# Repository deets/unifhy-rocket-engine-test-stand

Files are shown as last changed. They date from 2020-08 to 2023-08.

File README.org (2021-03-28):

* UNIFHY - universeller Prüfstand für Feststoff- und Hybridmotoren

Ziel dieses Projektes ist die Entwicklung eines preiswerten
Prüfstandes mit einem Preis von maximal 500 EUR.

Der Prüfstand besteht aus drei Modulen:

 - Modul 1: einem aus ITEM Prüfbalken bestehenden mechanischen Aufbau.
 - Modul 2: einer Prüfbox zur Datenaufnahme, Speicherung, Übermittlung und
   gegebenenfalls Fernsteuerung.
 - Modul 3: einer Software zur Konfiguration, Datenerfassung und Auswertung von Modul 2.

Hier die [[file:doc/Pruefstand_UNIFHY.pdf][Anforderungen erhoben am 22.02.2020]].

** Modul 1 - Teststand

Ein Aufbau des Testands von Andreas:

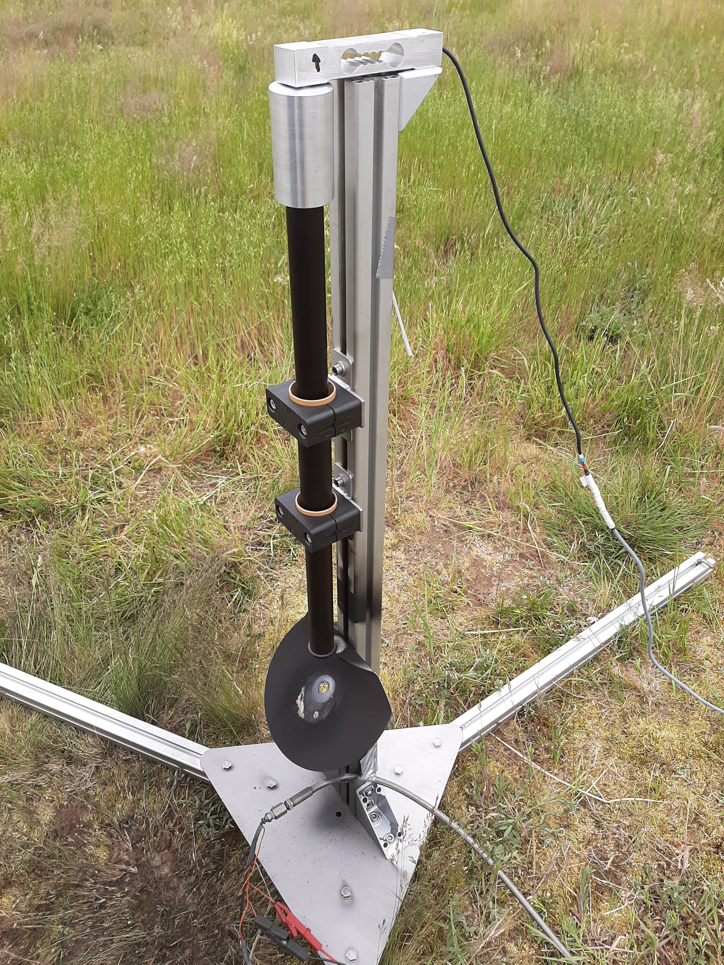
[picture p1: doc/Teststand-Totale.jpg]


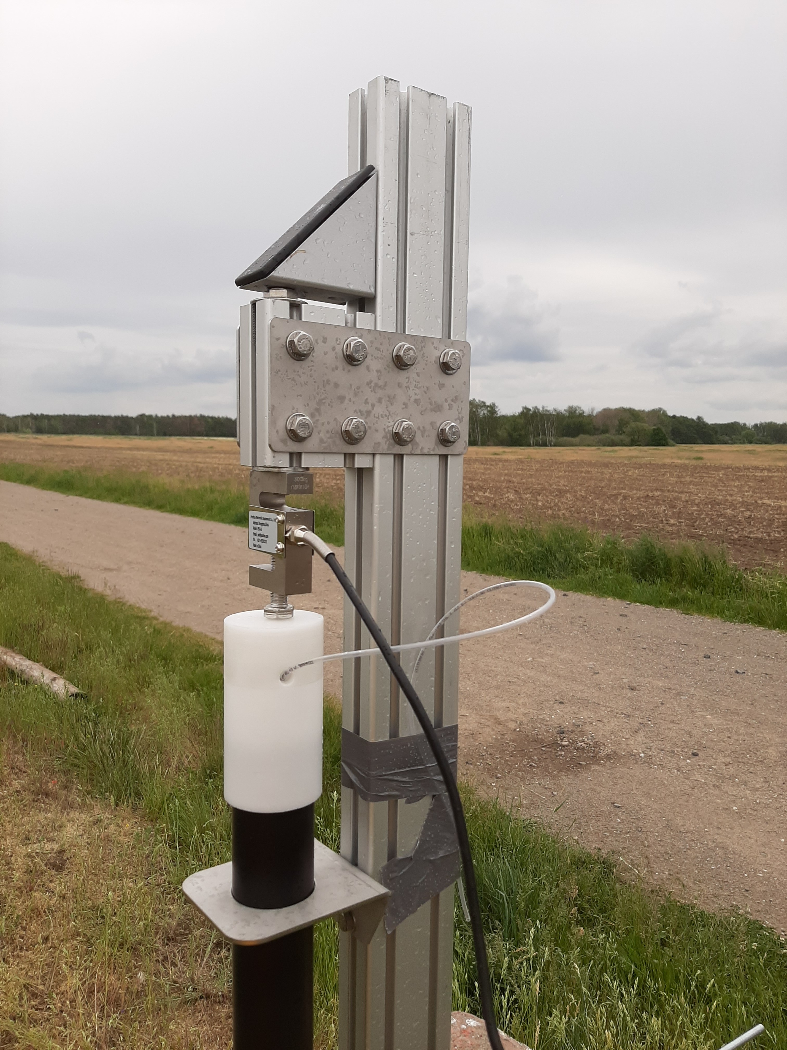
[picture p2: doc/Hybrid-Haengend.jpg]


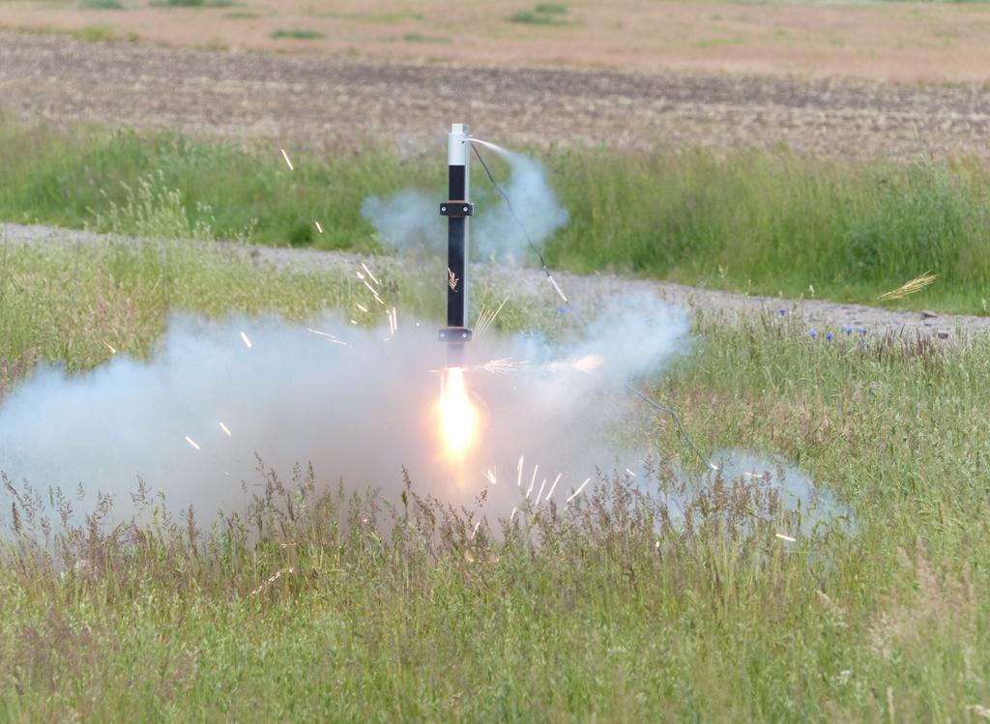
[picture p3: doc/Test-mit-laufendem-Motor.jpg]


** Modul 2 - Firmware

*** ADS1256 Breakout Board

Pin out of the breakout board as seen from top with control interface
to the left:

|-----+----------+---------|
| Pin | Function | P2 Eval |
|-----+----------+---------|
|   1 | PDWN     |      21 |
|   2 | CS_      |      20 |
|   3 | DRDY     |      19 |
|   4 | DOUT     |      17 |
|   5 | DIN      |      18 |
|   6 | SCLK     |      16 |
|   7 | GND      |     GND |
|   8 | 5V       |     EXT |
|-----+----------+---------|

#+attr_html: :width 400 px
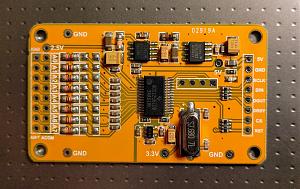
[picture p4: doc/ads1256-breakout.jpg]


** GIT Konfiguration

Wir arbeiten mit einem [[https://medium.com/singlestone/a-git-workflow-using-rebase-1b1210de83e5][rebase]] basierten GIT workflow. Dazu ist es
hilfreich eine Reihe von Einstellungen vorzunehmen. Die folgenden
Kommandos werden in einer Shell eingegeben, und man muss sich in
der Arbeitskopie befinden:

#+begin_src bash
git config pull.rebase true
#+end_src

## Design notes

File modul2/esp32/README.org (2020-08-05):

* Unifhy ESP32

A small test of the realtime capabilities of the ESP32 whilst
peforming writes to an SD-card and running a WIFI connection.

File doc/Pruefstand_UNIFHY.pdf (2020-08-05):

## Anforderungen an einen universellen Prüfstand für Feststoff- und Hybridmotoren

### Arbeitstitel: UNIFHY, Stand: 22.02.2020

Grundsätzliches:
–Materialpreis max. EUR 500,-
–Der Prüfstand besteht aus ITEM-Prüfbalken (Modul 1), Prüfbox für den Feldeinsatz (Modul 2) und Konfigurations- und Auswertesoftware für PC (Modul 3)
–Der Prüfbalken soll durch verschiedene Aufnahmen sowohl senkrecht, als auch waagerecht und „über Kopf“ positioniert werden können.
–Die Prüfbox soll sowohl alleine (mit kleinem LC-Display und Menüsteuerung, ähnlich der vieler 3D-Drucker), als auch mit Funk- oder USB-Verbindung zu einem Laptop, auf dem Modul 3 läuft, nutzbar sein.
–Bohrungen, Durchgänge, Steckverbindungen, Aufnahmen sollen standardisiert (und wetterfest) sein.
–aktuell mögliche Anzahl an Prüfständen: 7
–Für die Bedienung des Prüfstandes (inkl. Software) soll ein Tutorial geschrieben werden.
–Eine möglichst lange gesicherte Verfügbarkeit von Ersatzteilen (auch im Elektronik-Bereich) sollte gewährleistet sein.
–Der Prüfstand soll leicht auf- und abzubauen sein und bei Transport und Lagerung wenig Platz beanspruchen.

Mechanik:
– Aufbau auf ITEM-Profil 40 mm * 80 mm.
– Fußkonstruktion individuell, abhängig davon, wie der Motor ausgerichtet sein soll.
– Motorbefestigung mit Schellen und passgenauen Ringen, dadurch auch Zentrierung des Motors unter dem Biegebalken.
– Ein Überlastungsschutz für den Biegebalken ist sinnnvoll / ggf. auch nicht sinnvoll, wenn der Biegebalken billig und leicht auszutauschen ist?
– Befestigung des Biegebalkens am ITEM-Profil
– Verankerung der Fußkonstruktion (individuell), Verspannung des ITEM-Profils
– leichter Aufbau, sichere Ersatzteilbeschaffung für die nächsten Jahre

Elektronik:
– Messbereiche: bis 2000 N, bis 500 N, bis 10 N (jeweils mit einem für diesen Messbereich geeigneten Biegebalken/DMS)
– Arduino-basiert - Mega, Maple oder Due?
–Aufzeichnungsrate: bis 2000/s
–Auflösung: min. 12 bit
- 4 Messkanäle: Schub, Brennkammerdruck, Tankdruck, Temperatur – RTC
– Optional: Preview der Schubkurve über einen Bondrucker

Software:
– Es soll ein Programm (Modul 3) geschrieben werden, das sowohl die Konfiguration der Prüfbox (Modul 2), als auch die Datenerfassung während des Tests, als auch die Auswertung der Schubkurven (einschließlich erzeugen einer *.eng-Datei) gestattet und zudem bedienerfreundlich ist.
– Die Auswertung der Schubkurve soll weitestgehend automatisiert sein, bestimmte Punkte (s. Anlage 1) sollen aber auswählbar sein.
– Der Aufzeichnungsbeginn soll einstellbar sein, ebenso das Aufzeichnungsende. Eine automatische Aufzeichnung der Schubdaten mehrere Sekunden VOR Motoranzündung soll möglich sein.
– Ein weiteres Programm ist notwendig für den Betrieb der Prüfbox (Modul 2).
– Die PC-Software (Modul 3) soll den Benutzer entlang einer Checkliste vom Kalibrieren des Prüfstandes über den Motortest bis zur Auswertung führen.
– Anzündung des Motors wahlweise über die PC-Software (Modul 3) ODER manuell.
– Als Startsignal für die Datenaufzeichnung soll sowohl ein Messwert (z.B. F > 1 N), als auch das manuelle Anzündsignal (Startknopf), als auch eine Benutzereingabe (zum Testen) möglich sein. – Teilautomatische, software-geführte Kalibrierung des Prüfstandes mit drei geeigneten Massestücken.
– Speicherung der Rohdaten als ASCII-Datei. Ebenso Datenübertragung.
– „Nullsetzen“ muss möglich sein.
– Speicherung aller Rohdaten auf SD-Karte in Modul 2; während des Tests werden nur die wichtigsten Daten bzw. eine reduzierte Datenmenge (z.B. jeder 10. Messwert) in Echtzeit an Modul 3 übertragen.
– Eine „Fernsteuerung“ von Modul 2 soll möglich sein (Funk / Leitung / WLAN?).

Anlage 1

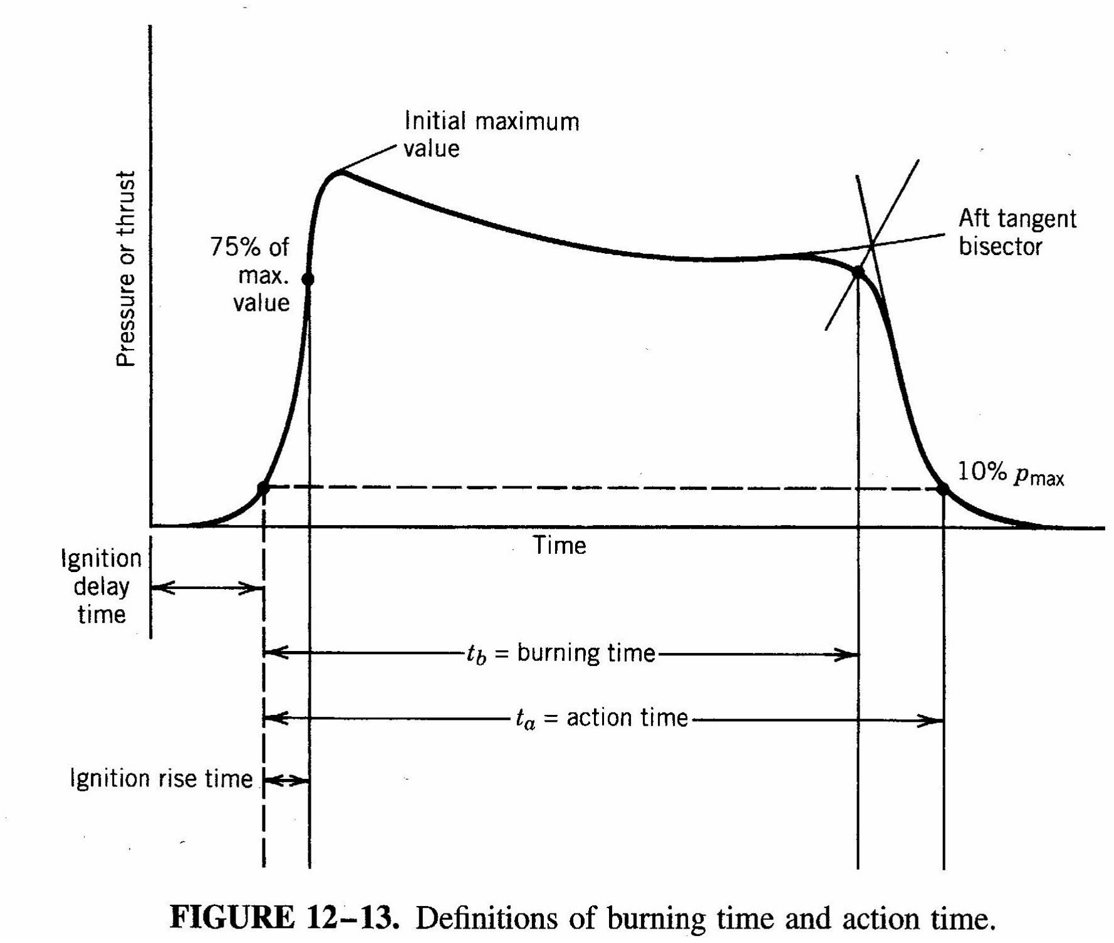
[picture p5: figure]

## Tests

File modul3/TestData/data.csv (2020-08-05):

Schub_x | Schub_y
0.0611 | -198.3902
0.1235 | -205.9467
0.1348 | -211.5601
0.1462 | -197.7425
0.1575 | -175.9366
0.1688 | -151.324
0.1802 | -170.1073
0.1915 | -187.8111
0.2028 | -197.3107
0.2142 | -248.479
0.2255 | -194.504
0.2368 | -218.4689
0.2482 | -233.1501
0.2595 | -201.1969
0.2708 | -216.7417
0.2822 | -199.9015
0.2935 | -233.5819
0.3048 | -140.529
0.3162 | -209.617
0.3275 | -203.3559
0.3389 | -129.5181
0.3502 | -291.659
0.3615 | -123.0411
0.3729 | -220.412
0.3842 | -181.3341
0.3955 | -152.4035
0.4069 | -281.0799
0.4182 | -148.0855
0.4295 | -252.1493
0.4409 | -136.211
0.4522 | -160.1759
0.4635 | -210.0488
0.4749 | -106.6327
0.4862 | -276.7619
0.4975 | -135.5633
0.5089 | -233.366
0.5202 | -206.8103
0.5316 | -153.2671
0.5429 | -264.6715
0.5542 | -120.6662
0.5656 | -285.8297
0.5769 | -169.4596
0.5882 | -183.4931
0.5996 | -239.843
0.6109 | -106.6327
0.6222 | -242.8656
0.6336 | -107.7122
0.6449 | -191.0496
0.6562 | -171.8345
0.6676 | -96.9172
0.6789 | -180.0387
0.6903 | -17.6819
0.7016 | -168.8119
0.7129 | -38.6242
0.7243 | -51.3623
0.7356 | -86.554
0.7469 | 75.1551
0.7583 | -69.0661
0.7696 | 91.7794
0.7809 | 29.3843
0.7924 | 29.6002
0.804 | 50.5425
0.8157 | -103.826
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

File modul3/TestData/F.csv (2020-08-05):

# Observable : F
# Unit       : none
# ID         : 0
#
# Calibration
#
# fitting function : linear
# parameters :
#
# a*x+b
# a = 0.00044840
# b = -9.76000000
# recorded events : 137071
#
0.060900  20.898902
0.123100  20.878275
0.134400  20.933877
0.145700  20.855407
0.157000  20.810567
0.168300  20.882311
0.179600  20.928944
0.190900  20.901144
0.202100  20.913250
0.213400  20.939706
0.224700  20.883656
0.236000  20.896211
0.247300  20.908318
0.258600  20.876482
0.269900  20.800254
0.281200  20.817293
0.292500  20.858994
0.303800  20.930290
0.315100  20.962126
0.326400  20.898902
0.337700  20.946880
0.349000  20.998446
0.360300  20.953606
0.371600  20.847784
0.382900  20.828054
0.394200  20.926254
0.405500  20.839713
0.416800  20.850923
0.428100  20.869307
0.439300  20.856304
0.450600  20.906524
0.461900  20.951813
0.473200  21.011898
0.484500  20.959436
0.495800  20.878724
0.507100  20.893521
0.518400  20.876033
0.529700  20.878724
0.541000  20.894418
0.552300  20.833884
0.563600  20.928048
0.574900  20.945984
0.586200  20.911457
0.597500  20.885450
0.608800  20.972439
0.620100  20.996653
0.631400  20.983201
0.642700  20.910112
0.654000  20.839264
0.665300  20.955848
0.676600  20.974681
0.687800  20.887243
0.699100  20.908318
0.710400  20.899798
0.721700  20.913250
0.733000  20.933428
0.744300  20.934325
0.755600  20.900247
0.766900  20.902040
0.778200  20.853165
0.789700  20.848232
0.801300  20.918183
0.812900  20.915941
0.824400  20.912354
0.836000  20.877827
0.847600  20.828503
0.859100  20.858097
0.870700  20.880517
0.882300  20.906524
0.893800  20.891279
0.905400  20.882311
0.917000  20.954055
0.928600  20.955400
0.940100  20.971094
0.951700  20.993066
0.963300  20.876482
0.974800  20.842403
0.986400  20.906076
0.998000  20.954952
1.009500  20.901592
1.021100  20.888588
1.032600  20.925357
1.044200  20.882311
1.055800  20.923115
1.067400  20.921770
1.078900  20.908766
1.090500  20.917734
1.102100  20.885898
1.113600  20.870652
1.125200  20.963471
1.136800  20.936567
1.148400  20.898902
1.159900  20.914596
1.171500  20.842852
1.183100  20.898902
1.194600  20.947329
1.206200  20.967058
1.217800  20.963471
1.229300  20.952710
1.240900  20.951364
1.252500  20.923115
1.264000  20.870652
1.275600  20.822674
1.287200  20.787250
1.298800  20.890382
1.310300  20.983201
1.321900  20.950916
1.333500  20.902937
1.345000  20.872446
1.356600  20.915044
1.368100  20.931186
1.379700  20.923564
1.391300  20.939706
1.402900  20.871998
1.414400  20.895314
1.426000  20.941051
1.437600  20.902040
1.449100  20.914147
1.460700  20.833884
1.472300  20.827158
1.483800  20.915492
1.495400  20.932980
1.507000  20.938809
1.518500  20.924460
1.530100  20.931186
1.541700  20.935670
1.553300  20.949571
1.564800  20.971542
1.576400  20.929393
1.588000  20.905628
1.599500  20.915044
1.611100  20.932980
1.622700  20.892176
1.634200  20.932083
1.645800  20.994859
1.657400  20.950019
1.668900  20.918631
1.680500  20.901144
1.692100  20.858097
1.703600  20.845542
1.715200  20.887243
1.726800  20.921770
1.738400  20.924012
1.749900  20.940154
1.761500  20.902937
1.773100  20.897556
1.784600  20.922667
1.796200  20.941500
1.807800  20.905179
1.819300  20.952710
1.830900  20.959884
1.842500  20.973784
1.854100  20.946432
1.865600  20.827158
1.877200  20.873343
1.888800  20.914147
1.900300  20.939258
1.911900  20.906524
1.923500  20.876482
1.935000  20.886795
1.946600  20.952710
1.958200  20.959884
1.969700  20.912802
1.981300  20.941051
1.992900  20.927151
2.004500  20.905179
2.016000  20.956745
2.027600  21.007863
2.039100  20.943293
2.050700  21.008760
2.062300  20.976475
2.073900  20.911905
2.085400  20.945087
2.097000  20.853165
2.108600  20.910560
2.120100  20.930738
2.131700  20.940603
2.143300  20.937912
2.154900  20.962126
2.166400  20.947777
2.178000  20.928944
2.189600  20.941051
2.201100  21.002930
2.212800  20.967507
2.224300  20.916389
2.235800  20.958987
2.247400  20.940603
2.259000  20.967058
2.270600  21.002482
2.282100  21.060774
2.293700  20.980959
2.305300  20.936119
2.316800  20.956297
2.328400  20.930738
2.340000  20.925806
2.351500  20.918631
2.363100  20.914596
2.374700  20.933877
2.386200  20.939706
2.397800  20.888588
2.409400  20.846887
2.421000  20.917734
2.432500  20.979165
2.444100  20.976923
2.455700  20.923564
2.467200  20.909215
2.478800  20.902489
2.490400  20.918631
2.501900  20.892176
2.513500  20.950468
2.525100  21.003379
2.536600  21.006966
2.548200  21.039251
2.559800  20.961678
2.571300  20.920425
2.582900  20.918183
2.594500  20.919080
2.606100  20.997550
2.617600  21.013692
2.629200  20.944190
2.640800  20.885450
2.652300  20.936119
2.663900  20.985891
2.675500  20.950019
2.687200  20.926702
2.698600  20.922667
2.710200  20.919528
2.721800  20.930738
2.733300  20.924012
2.744900  20.955400
2.756500  20.944638
2.768000  20.917734
2.779600  20.903386
2.791200  20.909663
2.802700  20.896211
2.814300  20.954503
2.825900  20.915941
2.837400  20.964368
2.849000  20.971542
2.860600  20.906973
2.872100  20.933428
2.883700  20.932980
2.895300  20.931186
2.906800  20.941948
2.918400  20.942845
2.930000  21.001585
2.941600  20.917286
2.953100  20.858994
2.964700  20.885898
2.976300  20.952710
2.987800  20.987236
2.999400  21.008311
3.011000  20.956745
3.022500  20.931186
3.034100  20.906524
3.045700  20.887692
3.057200  20.909215
3.068800  20.880966
3.080400  20.899350
3.091900  20.923115
3.103500  20.937464
3.115100  20.903834
3.126700  20.902489
3.138200  20.934325
3.149800  20.963023
3.161400  20.946880
3.173000  20.965265
3.184500  20.897108
3.196100  20.926702
3.207700  20.943293
3.219200  20.910112
3.230800  20.895314
3.242400  20.963023
3.253900  20.964816
3.265500  20.949571
3.277100  20.904731
3.288700  20.928048
3.300200  20.950468
3.311800  20.947777
3.323400  20.986340
3.334900  20.975578
3.346500  20.938809
3.358100  20.961678
3.369600  20.972439
3.381200  20.953606
3.392800  20.925357
3.404300  20.951813
3.415900  20.947777
3.427500  20.931186
3.439100  20.945984
3.450600  20.899350
3.462200  20.946880
3.473800  20.948674
3.485300  20.960781
3.496900  20.944190
3.508500  20.935670
3.520100  20.866617
3.531600  20.925357
3.543200  20.912354
3.554800  20.981856
3.566300  20.974681
3.577900  20.940154
3.589500  20.930290
3.601000  20.939258
3.612600  20.913699
3.624200  20.902040
3.635700  20.911905
3.647300  20.948226
3.658900  20.905628
3.670500  20.834780
3.682000  20.891727
3.693600  20.938361
3.705200  20.909215
3.716700  20.931635
3.728300  20.896211
3.739900  20.894418
3.751400  20.985443
3.763000  20.967955
3.774600  20.956745
3.786100  20.958987
3.797700  20.925357
3.809300  20.932980
3.820800  20.939706
3.832400  20.900695
3.844000  20.937464
3.855500  21.012347
3.867100  20.965713
3.878700  20.984994
3.890300  20.958090
3.901800  20.962126
3.913400  20.972888
3.925000  20.955400
3.936500  20.941500
3.948100  20.908318
3.959700  20.925806
3.971200  20.958539
3.982800  20.963023
3.994400  21.013244
4.005900  20.972439
4.017500  20.872446
4.029100  20.915492
4.040600  20.991720
4.052200  20.978717
4.063800  20.963920
4.075300  20.931186
4.086900  20.941051
4.098500  20.934774
4.110100  20.896660
4.121700  20.871101
4.133200  20.916838
4.144800  20.928496
4.156300  20.876482
4.167900  20.871998
4.179500  20.929393
4.191100  20.913699
4.202600  20.859891
4.214200  20.972439
4.225800  20.984546
4.237300  20.985443
4.248900  20.988133
4.260500  20.926254
4.272000  20.899798
4.283600  20.898902
4.295200  20.962126
4.306700  20.982304
4.318300  21.036560
4.329900  20.984098
4.341500  20.945535
4.353000  20.933428
4.364600  20.934325
4.376200  20.937912
4.387700  21.019970
4.399300  20.967955
4.410900  20.916838
4.422400  20.921770
4.434000  20.935222
4.445600  20.920873
4.457100  20.897108
4.468700  20.938809
4.480300  20.896660
4.491900  20.942845
4.503400  21.029834
4.515000  21.063016
4.526600  20.982304
4.538100  20.876033
4.549700  20.853165
4.561300  20.917734
4.572800  20.901144
4.584400  20.922667
4.596100  20.896211
4.607600  20.937016
4.619100  20.968404
4.630700  20.952261
4.642300  20.936567
4.653800  20.989478
4.665400  21.002930
4.677000  20.999343
4.688600  20.871998
4.700100  20.853613
4.711700  20.906973
4.723300  20.955848
4.734800  20.937912
4.746400  20.935670
4.758000  20.931635
4.769500  20.939706
4.781100  20.991720
4.792700  20.958987
4.804300  20.931186
4.815800  20.942396
4.827400  20.996653
4.839000  20.987685
4.850500  20.923115
4.862100  20.912802
4.873700  20.954055
4.885200  20.994859
4.896800  20.952710
4.908400  20.905179
4.920000  20.933428
4.931500  20.933877
4.943100  20.899798
4.954700  20.937912
4.966200  20.960781
4.977800  20.887243
4.989400  20.941500
5.001000  20.968404
5.012500  20.931635
5.024100  20.864823
5.035600  20.908766
5.047200  20.930738
5.058800  20.867962
5.070500  20.862133
5.081900  20.899798
5.093500  20.976475
5.105000  20.961229
5.116600  20.924460
5.128200  20.904282
5.139800  20.898005
5.151300  20.893969
5.162900  20.941500
5.174500  20.961229
5.186000  20.982304
5.197600  20.993514
5.209200  20.984546
5.220700  20.979614
5.232300  20.939706
5.243900  20.948226
5.255400  20.979165
5.267000  20.944190
5.278600  20.941500
5.290200  20.910560
5.301700  20.905628
5.313300  20.878724
5.324900  20.898902
5.336400  20.909215
5.348000  20.954055
5.359600  20.943293
5.371100  20.889934
5.382700  20.866168
5.394300  20.871998
5.405800  20.930290
5.417400  20.901144
5.429000  20.967955
5.440500  20.970646
5.452100  20.914596
5.463700  20.891279
5.475200  20.891727
5.486800  20.918631
5.498400  20.980510
5.510000  20.976923
5.521500  20.987236
5.533100  20.930738
5.544700  20.970197
5.556200  20.961229
5.567800  20.964368
5.579400  20.964816
5.590900  20.856304
5.602500  20.863926
5.614100  20.943293
5.625700  20.882311
5.637200  20.957194
5.648800  21.028938
5.660400  21.020418
5.671900  20.959436
5.683500  20.951813
5.695100  20.867962
5.706600  20.897108
5.718200  20.946880
5.729800  20.959884
5.741400  20.911457
5.752900  20.917734
5.764500  20.905179
5.776100  20.947777
5.787600  20.908766
5.799200  20.877827
5.810800  20.968404
5.822300  20.935222
5.833900  20.931186
5.845500  20.915941
5.857100  20.945087
5.868600  20.952261
5.880200  20.933877
5.891700  20.957194
5.903300  20.993066
5.914900  20.873343
5.926500  20.903386
5.938000  20.964816
5.949600  20.951364
5.961200  20.980510
5.972700  20.958539
5.984300  20.943293
5.995900  20.962574
6.007500  20.972888
6.019000  20.957642
6.030700  20.896211
6.042100  20.816396
6.053700  20.893072
6.065300  20.945984
6.076800  20.962126
6.088400  20.907870
6.100000  20.904731
6.111600  20.919528
6.123100  20.908318
6.134700  20.965265
6.146300  20.983201
6.157800  20.941948
6.169400  20.945087
6.181000  20.986340
6.192600  20.928496
6.204100  20.896660
6.215700  20.893969
6.227300  20.921322
6.238800  20.950468
6.250400  20.919080
6.262000  20.939706
6.273500  20.950019
6.285100  20.897556
6.296700  20.940603
6.308200  20.892176
6.319800  20.881862
6.331400  20.977820
6.342900  20.968852
6.354500  20.936119
6.366100  20.923115
6.377700  20.968404
6.389200  20.979614
6.400800  20.988582
6.412400  20.987685
6.423900  20.869307
6.435500  20.916838
6.447100  20.918631
6.458600  20.903386
6.470200  20.892176
6.481800  20.878724
6.493300  20.935222
6.504900  20.901592
6.516500  20.868859
6.528100  20.941948
6.539600  20.983201
6.551200  20.998895
6.562800  20.980510
6.574300  20.920425
6.585900  20.918631
6.597500  20.969749
6.609000  20.953158
6.620600  20.936567
6.632200  20.945087
6.643700  21.027592
6.655300  21.036560
6.666900  20.980510
6.678500  20.897108
6.690000  20.938361
6.701600  20.928496
6.713200  20.919528
6.724700  20.952710
6.736300  20.918631
6.747900  20.957642
6.759400  20.936119
6.771000  20.945984
6.782600  20.933428
6.794100  20.889934
6.805700  20.891279
6.817300  20.959884
6.828900  20.967058
6.840400  20.994411
6.852000  20.988133
6.863600  21.024454
6.875100  20.955400
6.886700  20.906524
6.898300  20.993514
6.909800  21.012795
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

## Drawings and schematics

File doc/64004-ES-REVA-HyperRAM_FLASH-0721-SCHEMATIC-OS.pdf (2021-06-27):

## HyperRAM and HyperFLASH

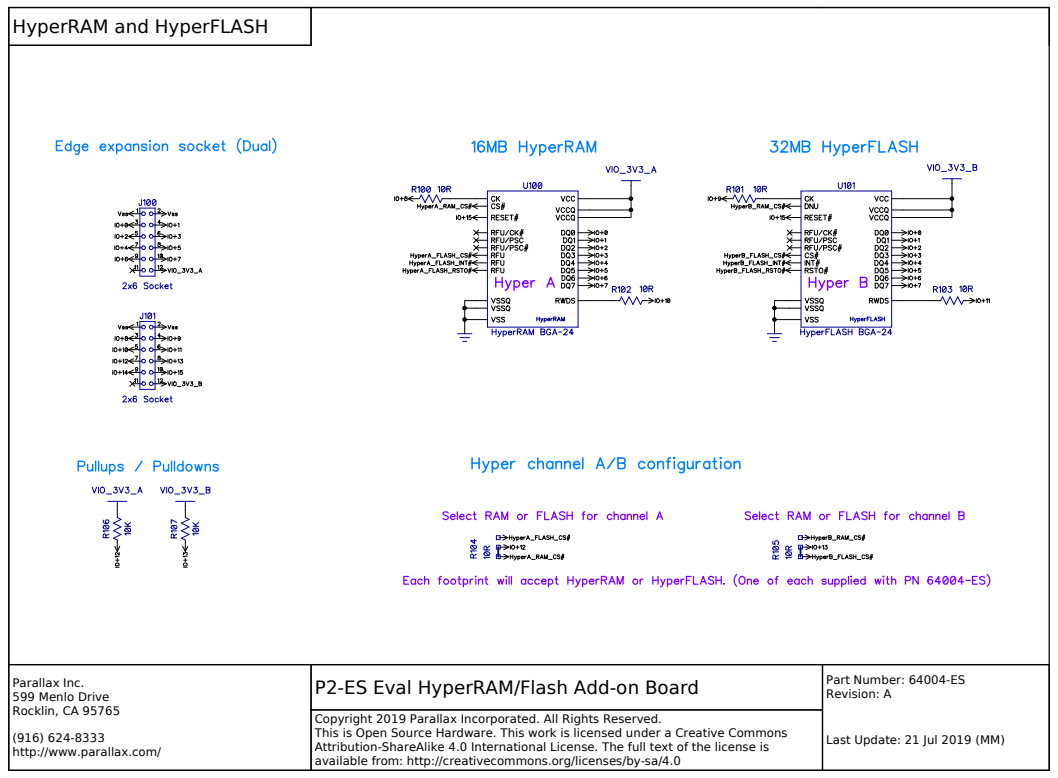
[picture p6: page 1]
P2-ES Eval HyperRAM/Flash Add-on Board; Part Number: 64004-ES; Revision: A; Parallax Inc. 599 Menlo Drive Rocklin, CA 95765

Copyright 2019 Parallax Incorporated. All Rights Reserved.
This is Open Source Hardware. This work is licensed under a Creative Commons
Attribution-ShareAlike 4.0 International License. The full text of the license is
available from: http://creativecommons.org/licenses/by-sa/4.0

http://www.parallax.com/

Last Update: 21 Jul 2019 (MM)

## Decoupling and Breakouts

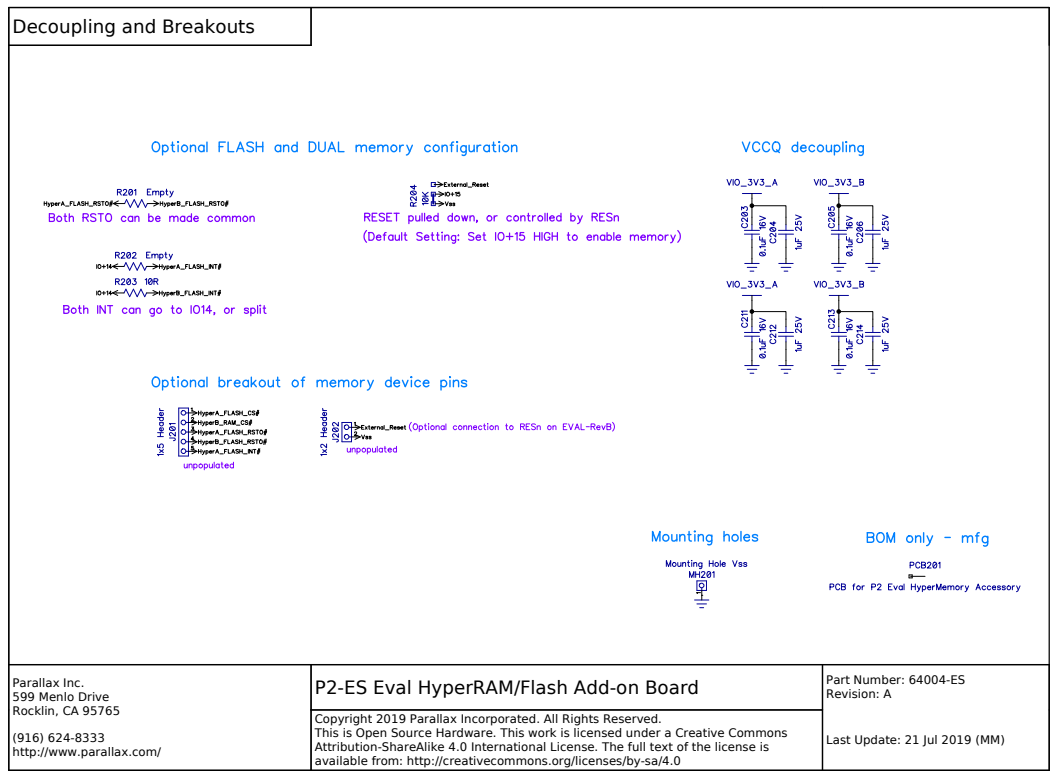
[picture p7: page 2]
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

## BOM

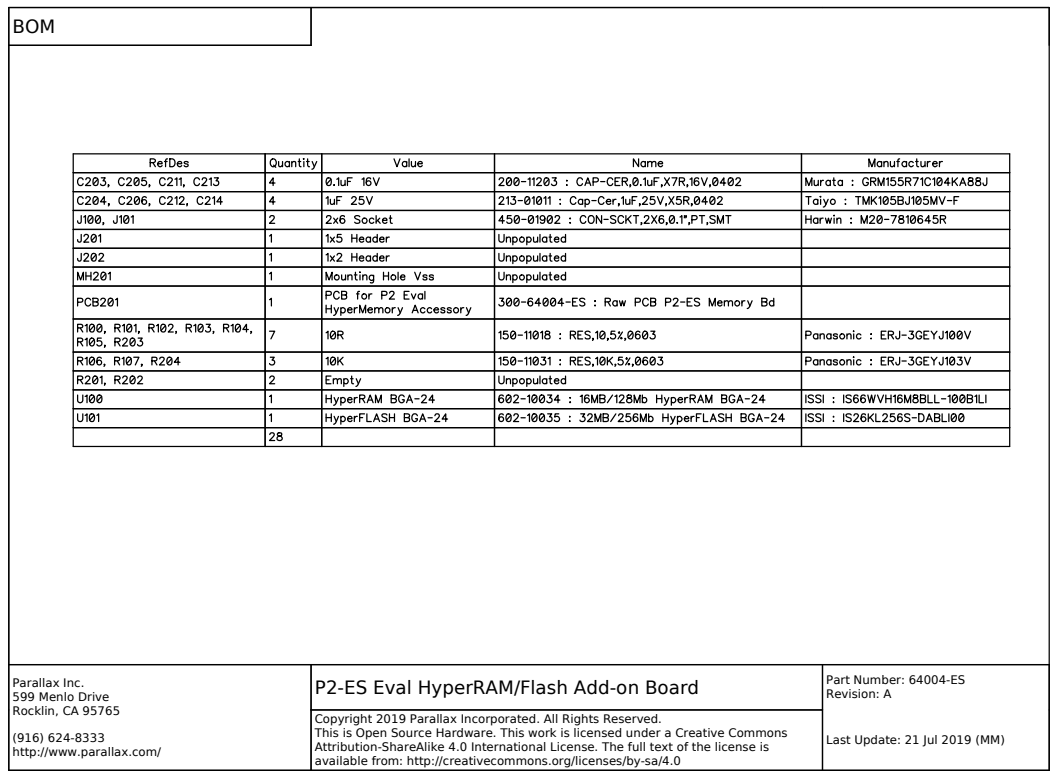
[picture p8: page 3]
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

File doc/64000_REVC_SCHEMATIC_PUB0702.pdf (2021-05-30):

## Microcontroller

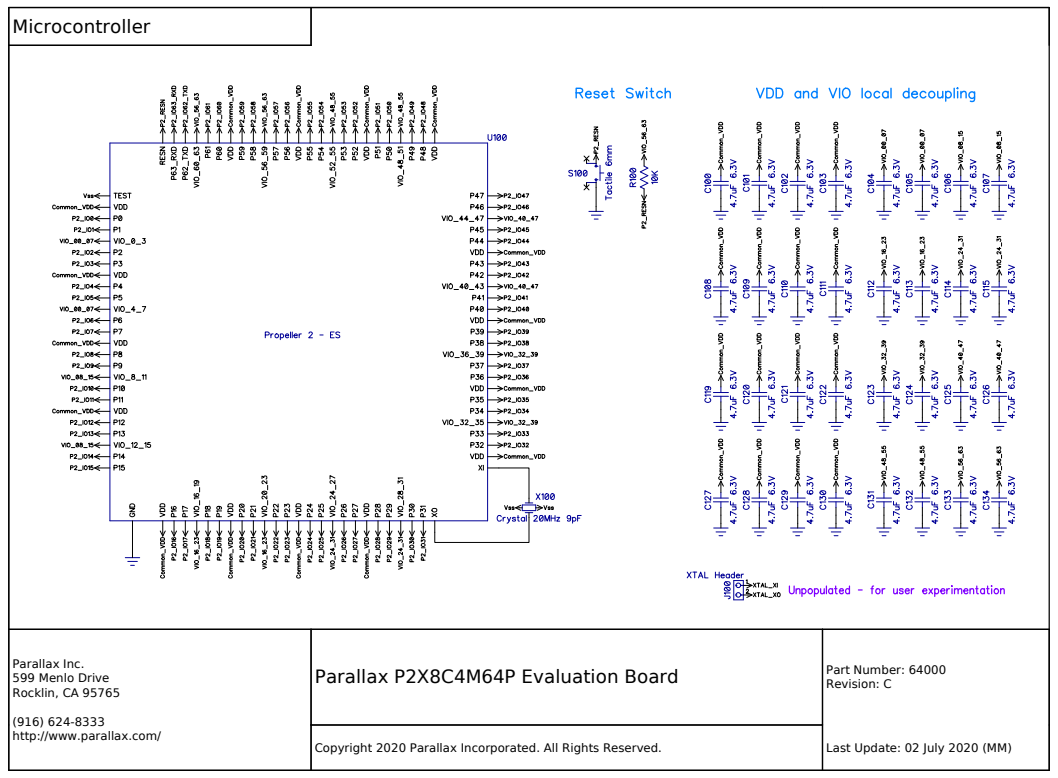
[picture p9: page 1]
Parallax P2X8C4M64P Evaluation Board; Part Number: 64000; Revision: C; Parallax Inc. 599 Menlo Drive Rocklin, CA 95765; Copyright 2020 Parallax Incorporated. All Rights Reserved.; Last Update: 02 July 2020 (MM)

http://www.parallax.com/

## I/O Headers

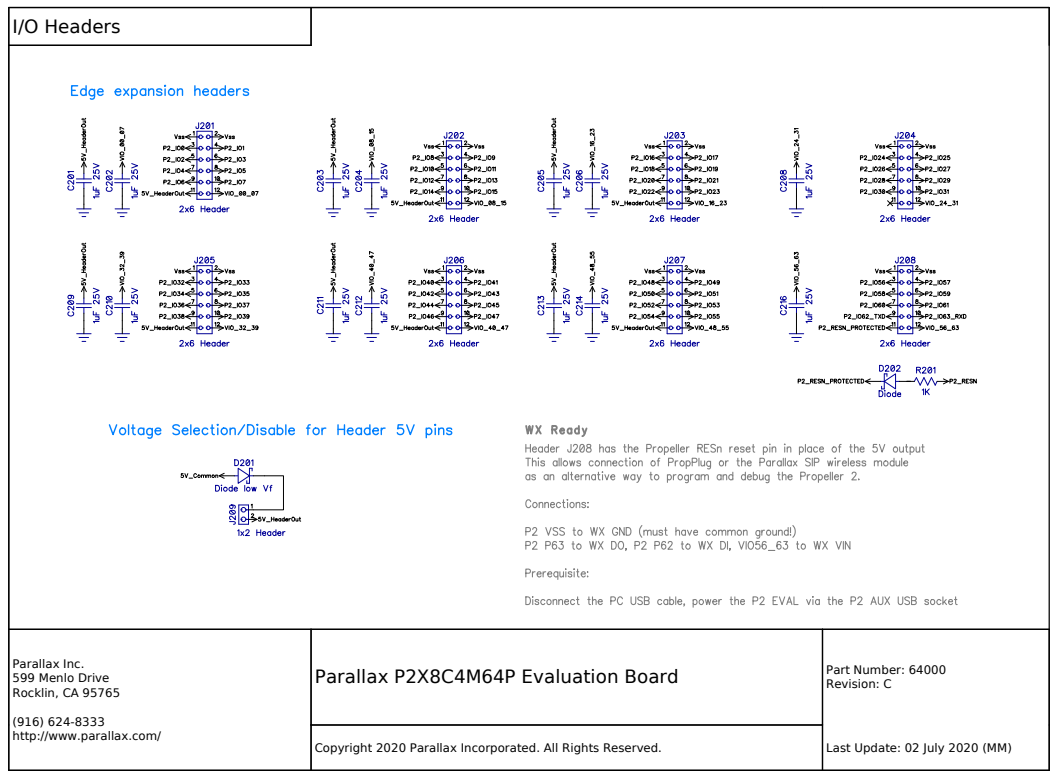
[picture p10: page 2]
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

## Memory

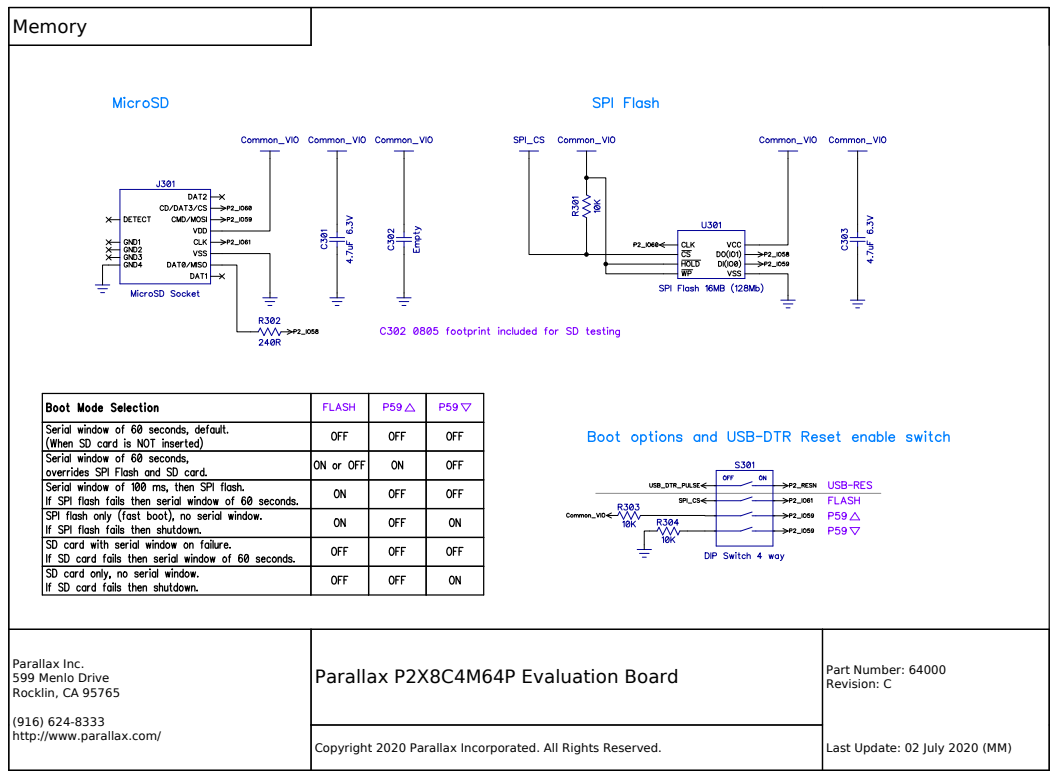
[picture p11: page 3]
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

## USB PC Socket

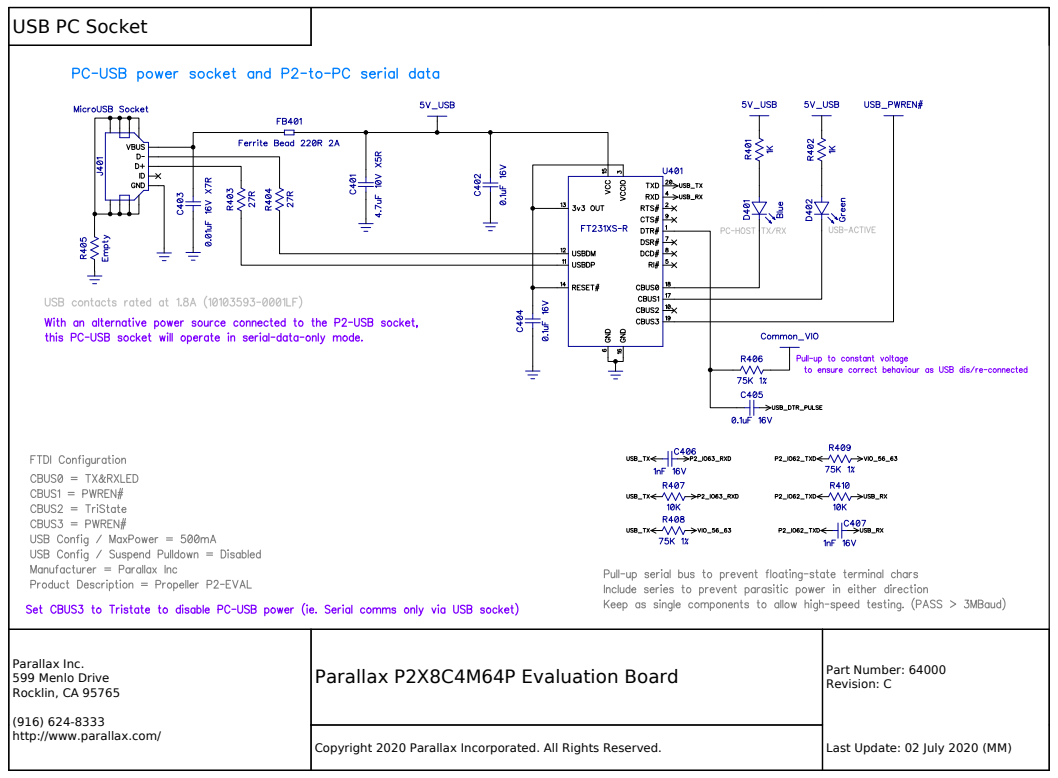
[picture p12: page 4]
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

## USB Aux Power Socket

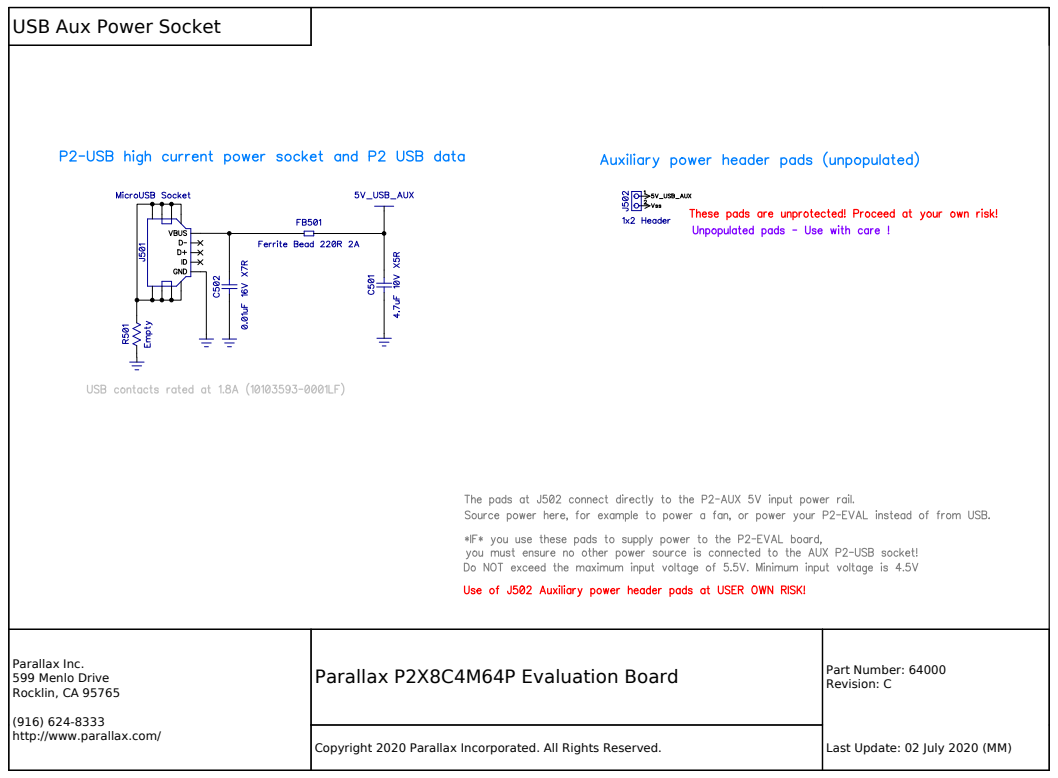
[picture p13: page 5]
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

## USB Current Limit and Logic

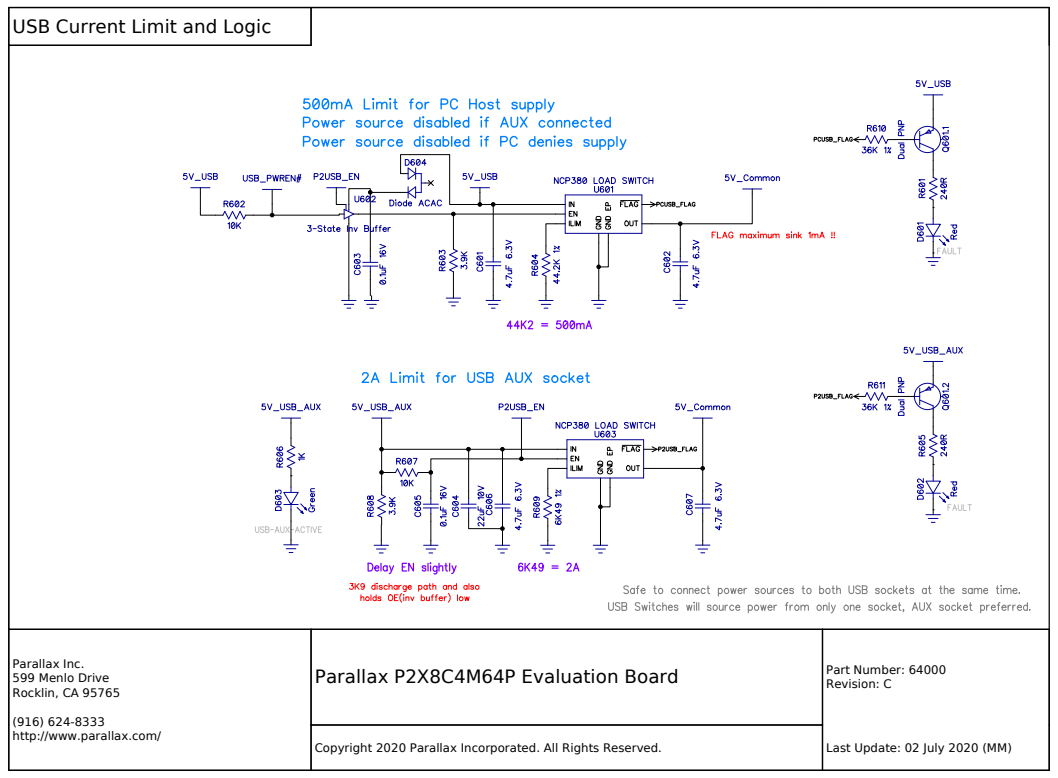
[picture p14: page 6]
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

## Common VDD 1V8

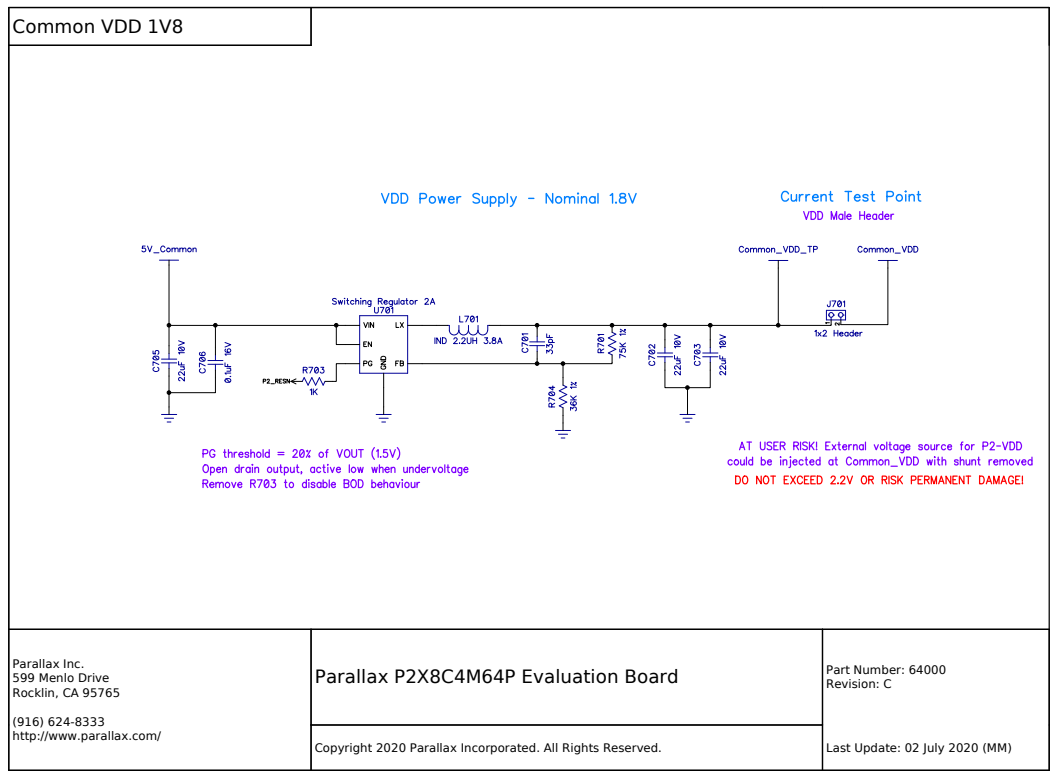
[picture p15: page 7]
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

## Common VIO 3V3

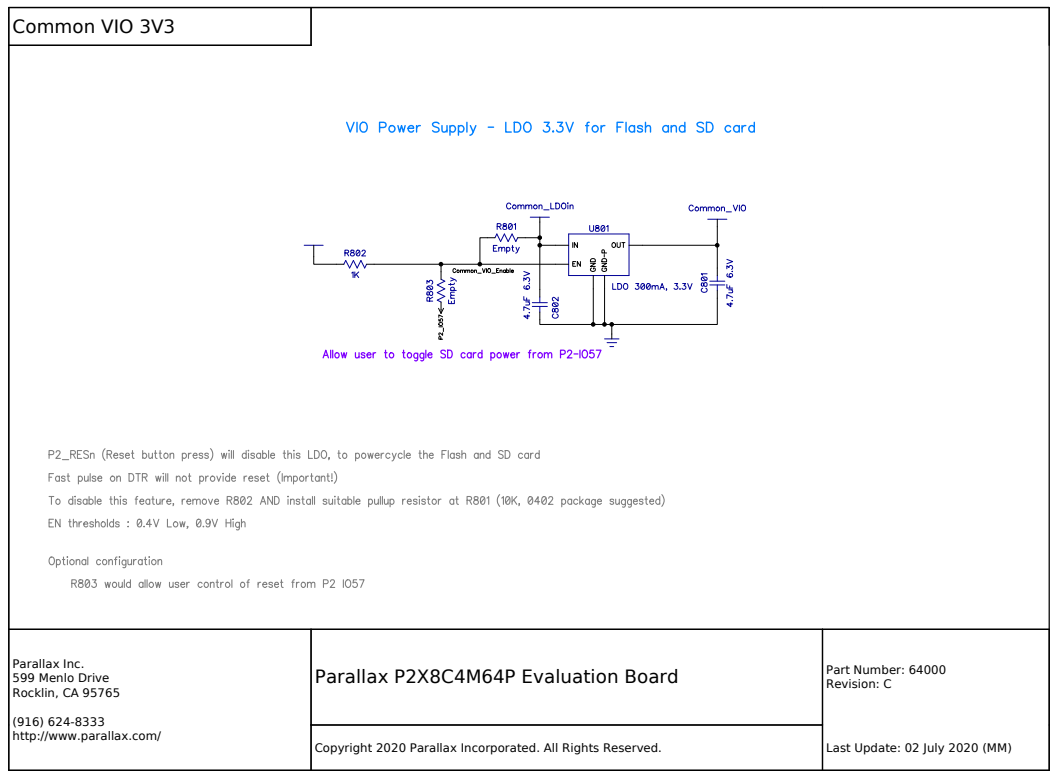
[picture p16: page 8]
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

## LDO 3V3

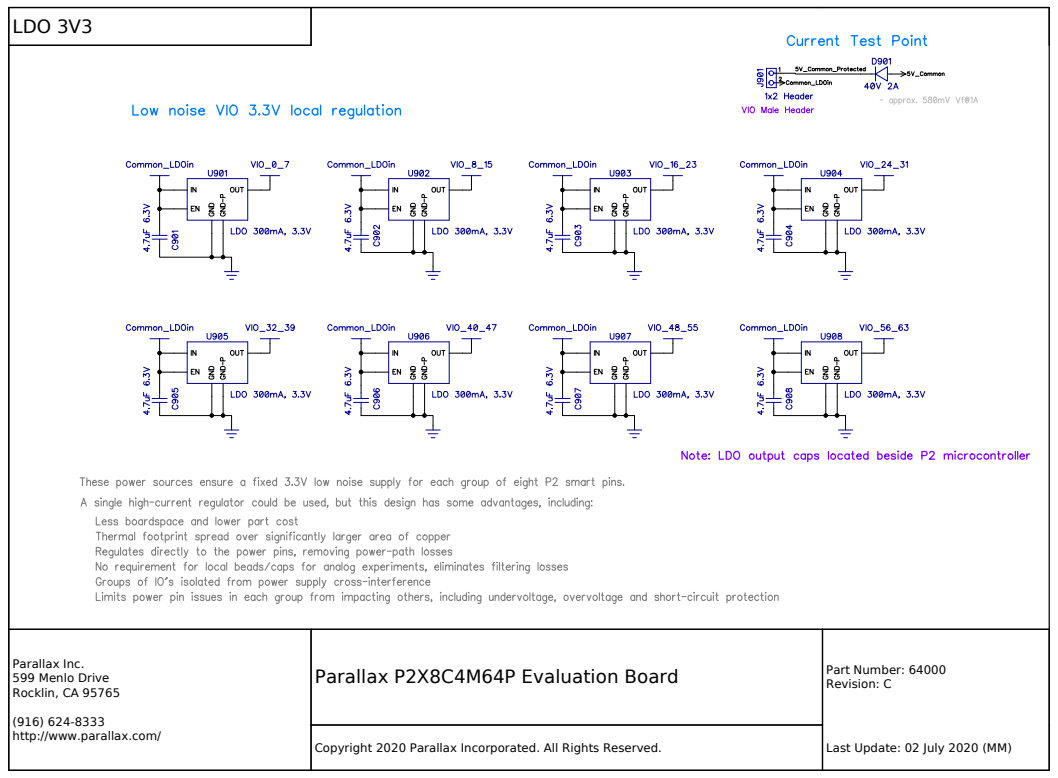
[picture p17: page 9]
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

## LEDs

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

## Misc

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

## BOM

Parallax P2X8C4M64P Evaluation Board | Part Number: 64000 Revision: C

Parallax Inc.
599 Menlo Drive
Rocklin, CA 95765


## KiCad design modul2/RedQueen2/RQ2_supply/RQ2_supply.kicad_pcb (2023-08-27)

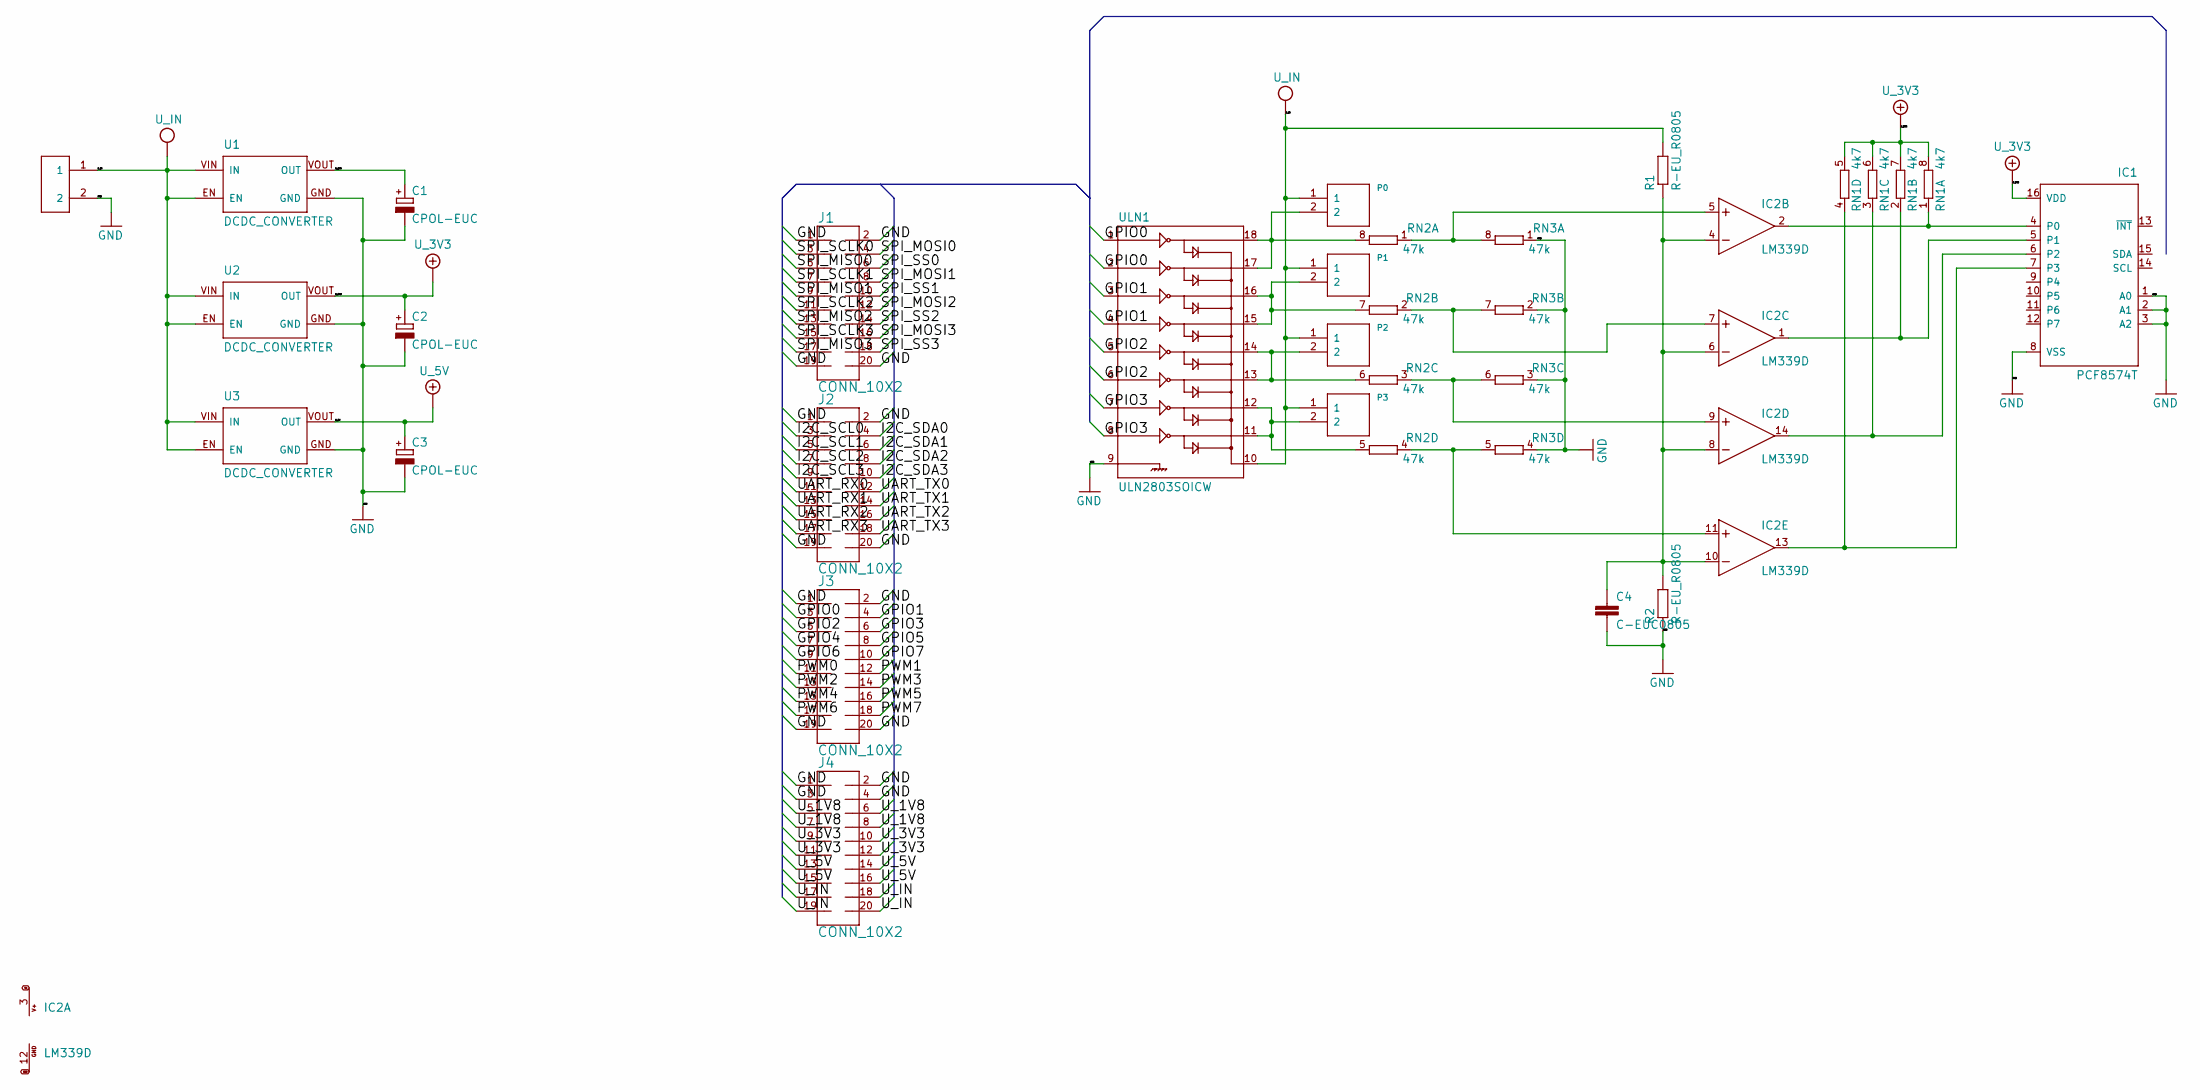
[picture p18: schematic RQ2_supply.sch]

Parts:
C1, C2, C3: CPOL-EUC; PANASONIC_C
C4: C-EUC0805; C0805
IC1: PCF8574T; SO16W
IC2: LM339D; SO14
J1, J2, J3, J4: CONN_10X2; 2X10
P0, P1, P2, P3: 2PIN; B2B-PH-K-S
R1, R2: R-EU_R0805; R0805
RN1: 4k7; 0603-ARV
RN2, RN3: 47k; 0603-ARV
U1, U2, U3: DCDC_CONVERTER
U$1: XT_CONN; XT30_PCB
ULN1: ULN2803SOICW; SO18L

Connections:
/GPIO0: J3.3, ULN1.1, ULN1.2
/GPIO1: J3.4, ULN1.3, ULN1.4
/GPIO2: J3.5, ULN1.5, ULN1.6
/GPIO3: J3.6, ULN1.7, ULN1.8
/GPIO4: J3.7
/GPIO5: J3.8
/GPIO6: J3.9
/GPIO7: J3.10
/I2C_SCL0: J2.3
/I2C_SCL1: J2.5
/I2C_SCL2: J2.7
/I2C_SCL3: J2.9
/I2C_SDA0: J2.4
/I2C_SDA1: J2.6
/I2C_SDA2: J2.8
/I2C_SDA3: J2.10
/PWM0: J3.11
/PWM1: J3.12
/PWM2: J3.13
/PWM3: J3.14
/PWM4: J3.15
/PWM5: J3.16
/PWM6: J3.17
/PWM7: J3.18
/SPI_MISO0: J1.5
/SPI_MISO1: J1.9
/SPI_MISO2: J1.13
/SPI_MISO3: J1.17
/SPI_MOSI0: J1.4
/SPI_MOSI1: J1.8
/SPI_MOSI2: J1.12
/SPI_MOSI3: J1.16
/SPI_SCLK0: J1.3
/SPI_SCLK1: J1.7
/SPI_SCLK2: J1.11
/SPI_SCLK3: J1.15
/SPI_SS0: J1.6
/SPI_SS1: J1.10
/SPI_SS2: J1.14
/SPI_SS3: J1.18
/UART_RX0: J2.11
/UART_RX1: J2.13
/UART_RX2: J2.15
/UART_RX3: J2.17
/UART_TX0: J2.12
/UART_TX1: J2.14
/UART_TX2: J2.16
/UART_TX3: J2.18
/U_1V8: C1.+, J4.5, J4.6, J4.7, J4.8, U1.VOUT (OUT)
GND: C1.-, C2.-, C3.-, C4.2, IC1.1 (A0), IC1.2 (A1), IC1.3 (A2), IC1.8 (VSS), IC2.12 (GND), J1.1, J1.2, J1.19, J1.20, J2.1, J2.2, J2.19, J2.20, J3.1, J3.2, J3.19, J3.20, J4.1, J4.2, J4.3, J4.4, R2.1, RN3.1, RN3.2 (1), RN3.3 (1), RN3.4 (1), U1.GND, U2.GND, U3.GND, U$1.2, ULN1.9
unnamed: C4.1, IC2.4 (-IN), IC2.6 (-IN), IC2.8 (-IN), IC2.10 (-IN), R1.1, R2.2
unnamed: IC1.4 (P0), IC2.2 (OUT), RN1.1
unnamed: IC1.5 (P1), IC2.1 (OUT), RN1.2 (1)
unnamed: IC1.6 (P2), IC2.14 (OUT), RN1.3 (1)
unnamed: IC1.7 (P3), IC2.13 (OUT), RN1.4 (1)
unnamed: IC2.5 (+IN), RN2.1, RN3.8 (2)
unnamed: IC2.7 (+IN), RN2.2 (1), RN3.7 (2)
unnamed: IC2.9 (+IN), RN2.3 (1), RN3.6 (2)
unnamed: IC2.11 (+IN), RN2.4 (1), RN3.5 (2)
unnamed: P0.2, RN2.8 (2), ULN1.17, ULN1.18
unnamed: P1.2, RN2.7 (2), ULN1.15, ULN1.16
unnamed: P2.2, RN2.6 (2), ULN1.13, ULN1.14
unnamed: P3.2, RN2.5 (2), ULN1.11, ULN1.12
U_3V3: C2.+, IC1.16 (VDD), J4.9, J4.10, J4.11, J4.12, RN1.5 (2), RN1.6 (2), RN1.7 (2), RN1.8 (2), U2.VOUT (OUT)
U_5V: C3.+, J4.13, J4.14, J4.15, J4.16, U3.VOUT (OUT)
U_IN: J4.17, J4.18, J4.19, J4.20, P0.1, P1.1, P2.1, P3.1, R1.2, U1.EN, U1.VIN (IN), U2.EN, U2.VIN (IN), U3.EN, U3.VIN (IN), U$1.1, ULN1.10
V+: IC2.3 (V+)

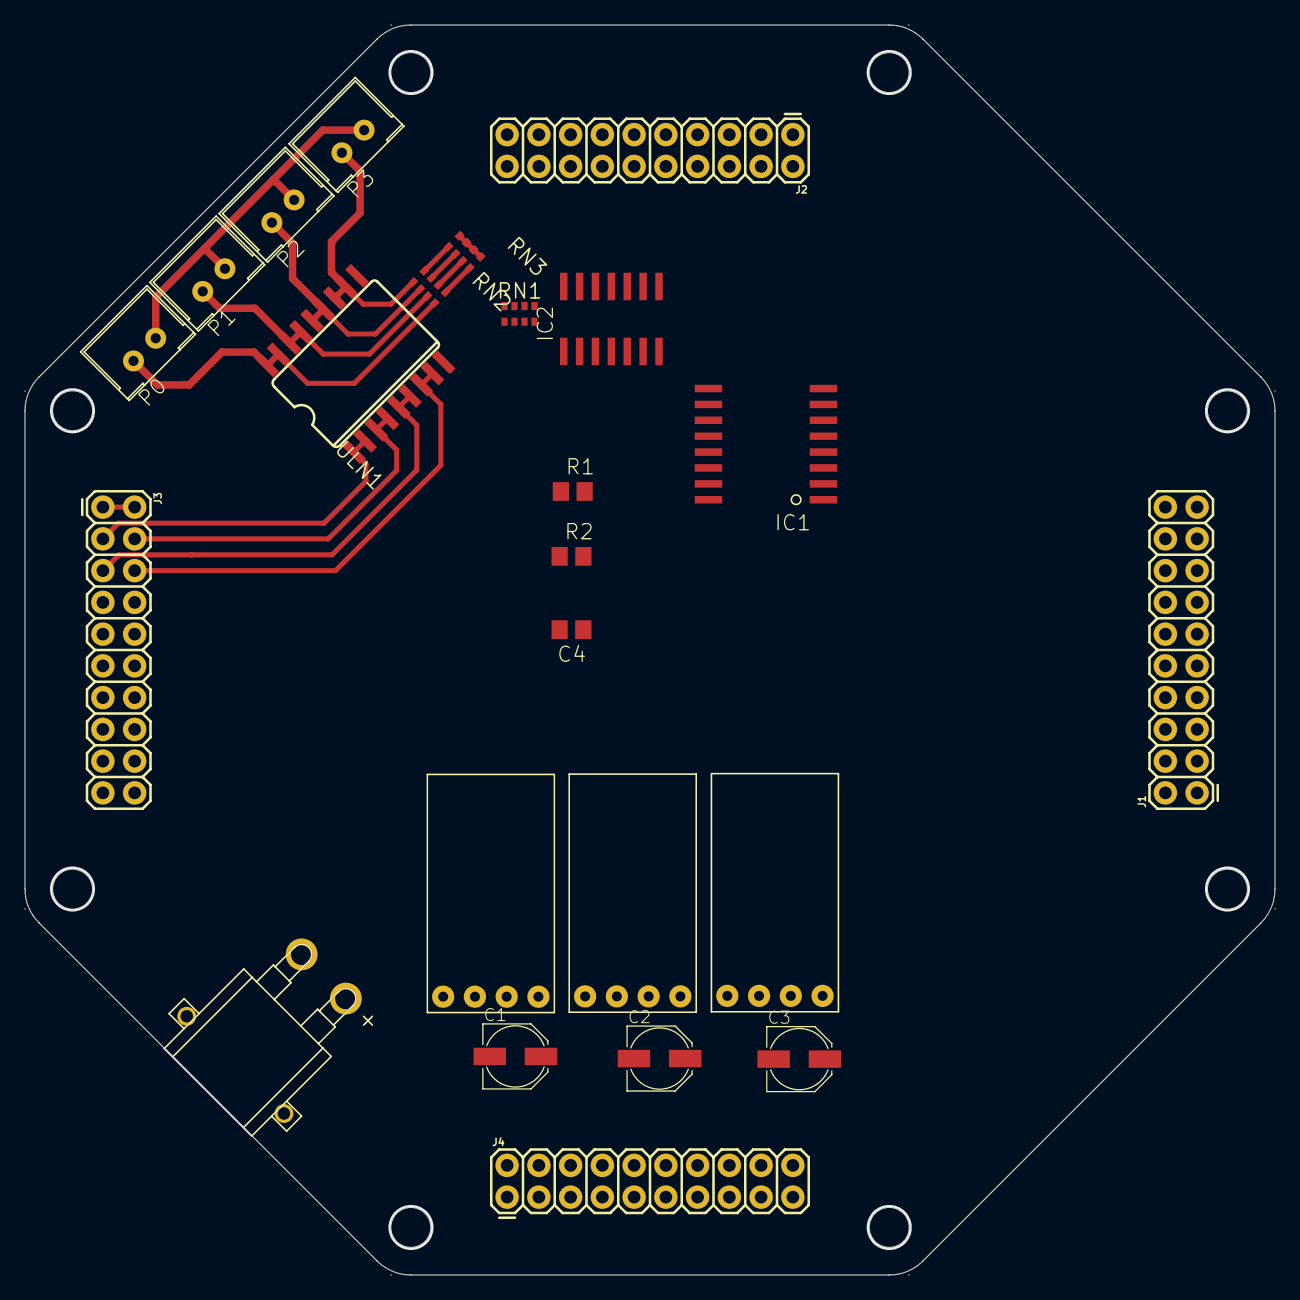
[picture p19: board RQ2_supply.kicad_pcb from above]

Board: 2 copper layers, 100.0 x 100.0 mm, 24 parts (0 on the bottom side), 22 nets.

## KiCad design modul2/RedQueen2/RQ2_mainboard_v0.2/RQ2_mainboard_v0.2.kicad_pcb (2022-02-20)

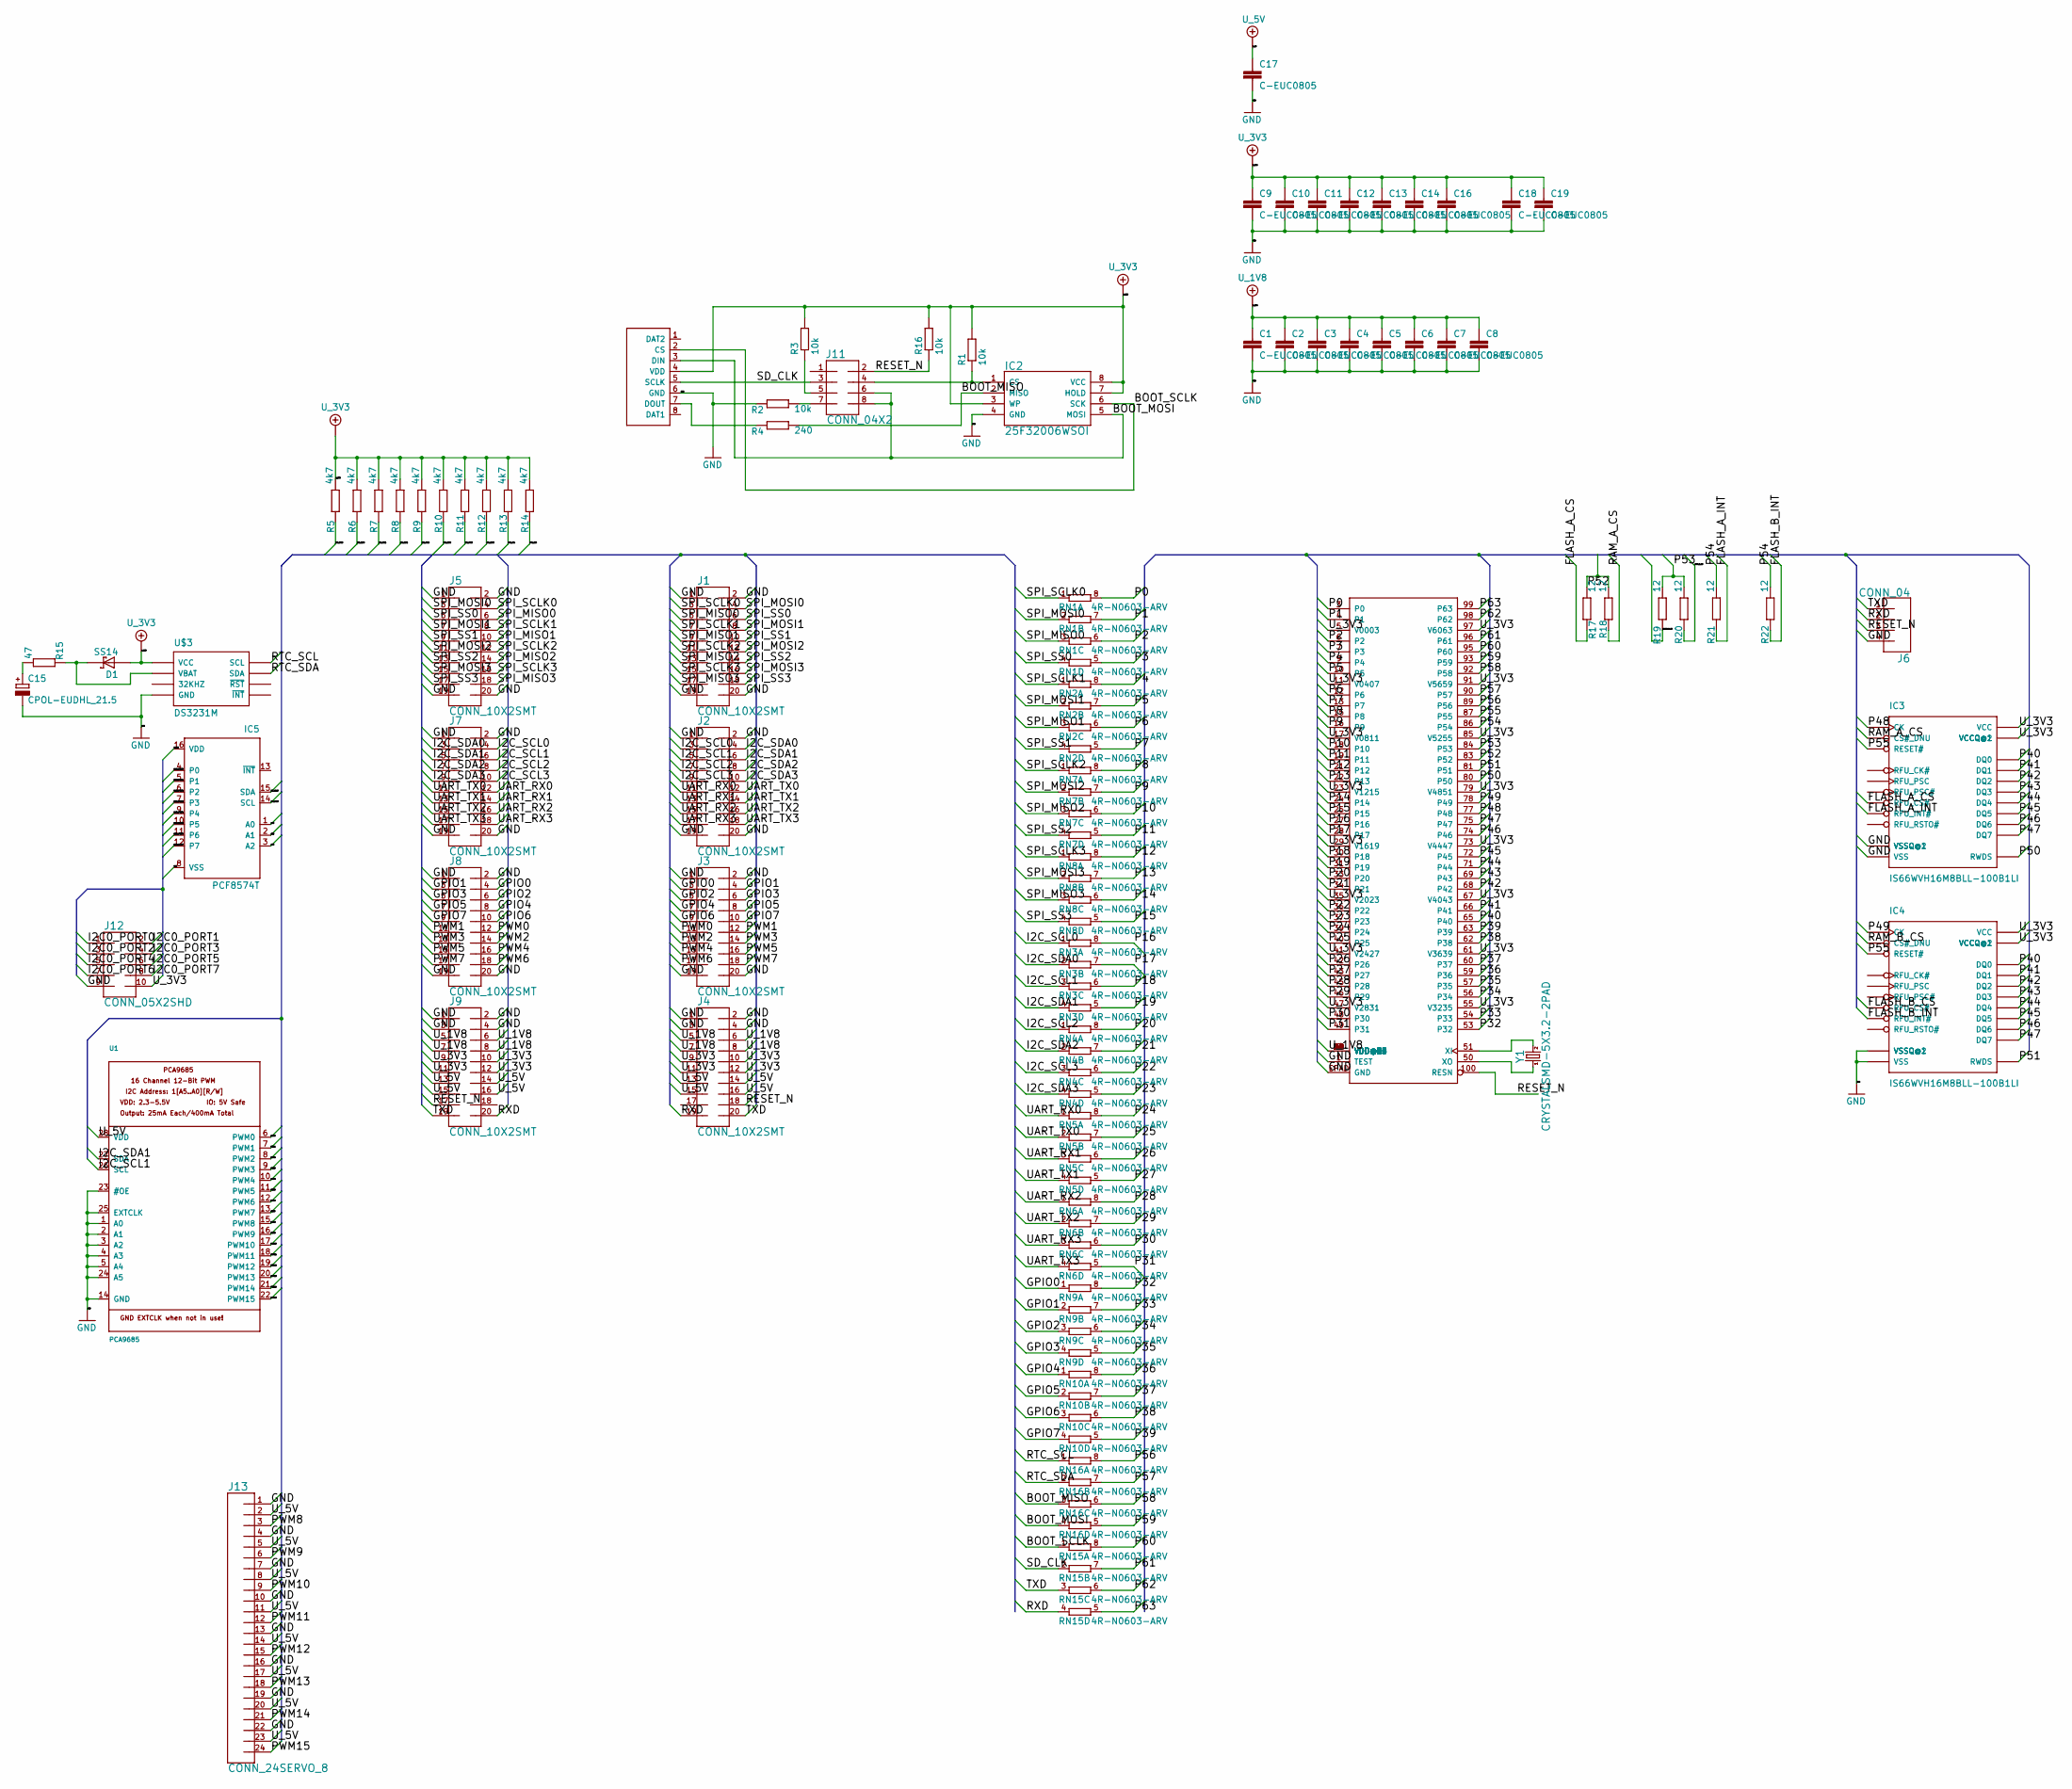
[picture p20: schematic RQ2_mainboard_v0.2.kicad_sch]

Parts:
C1, C2, C3, C4, C5, C6, C7, C8, C9, C10, C11, C12, C13, C14, C16, C17, C18, C19: C-EUC0805; C0805
C15: CPOL-EUDHL_21.5; DHL_21.5
D1: SS14; SMA_403D
IC1: P2X8C4M64P; TQFP100
IC2: 25F32006WSOI; SO08-EIAJ
IC3, IC4: IS66WVH16M8BLL-100B1LI; BGA-24
IC5: PCF8574T; SO16W
J1, J2, J3, J4, J5, J7, J8, J9: CONN_10X2SMT; 2X10_SMT
J6: CONN_04; 1X04
J11: CONN_04X2; 2X4
J12: CONN_05X2SHD; 2X5-SHROUDED
J13: CONN_24SERVO_8; 3X8
R1, R2, R3, R16: 10k; R0603
R4: 240; R0603
R5, R6, R7, R8, R9, R10, R11, R12, R13, R14: 4k7; R0603
R15: 47; R0603
R17, R18, R19, R20, R21, R22: 12; R0402
RN1, RN2, RN3, RN4, RN5, RN6, RN7, RN8, RN9, RN10, RN15, RN16: 4R-N0603-ARV; 0603-ARV
U1: PCA9685; TSSOP28
U$2: MICRO_SD_CONNECTORMOLEX_HINGE; MICRO_SD
U$3: DS3231M; SO-8
Y1: CRYSTALSMD-5X3.2-2PAD; CRYSTAL-SMD-5X3.2-2PAD

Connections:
/BOOT_MISO: IC2.2 (MISO), R4.1, RN16.3 (1)
/BOOT_MOSI: IC2.5 (MOSI), J11.6, J11.8, RN16.4 (1), U$2.3 (DIN)
/BOOT_SCLK: IC2.6 (SCK), RN15.1, U$2.2 (CS)
/FLASH_A_CS: IC3.C2 (RFU_CS#), R17.2
/FLASH_A_INT: IC3.A5 (RFU_INT#), R21.2
/FLASH_B_CS: IC4.C2 (RFU_CS#), R19.2
/FLASH_B_INT: IC4.A5 (RFU_INT#), R22.2
/GPIO0: J3.3, J8.4, RN9.1
/GPIO1: J3.4, J8.3, RN9.2 (1)
/GPIO2: J3.5, J8.6, RN9.3 (1)
/GPIO3: J3.6, J8.5, RN9.4 (1)
/GPIO4: J3.7, J8.8, RN10.1
/GPIO5: J3.8, J8.7, RN10.2 (1)
/GPIO6: J3.9, J8.10, RN10.3 (1)
/GPIO7: J3.10, J8.9, RN10.4 (1)
/I2C0_PORT0: IC5.4 (P0), J12.1
/I2C0_PORT1: IC5.5 (P1), J12.2
/I2C0_PORT2: IC5.6 (P2), J12.3
/I2C0_PORT3: IC5.7 (P3), J12.4
/I2C0_PORT4: IC5.9 (P4), J12.5
/I2C0_PORT5: IC5.10 (P5), J12.6
/I2C0_PORT6: IC5.11 (P6), J12.7
/I2C0_PORT7: IC5.12 (P7), J12.8
/I2C_SCL0: IC5.14 (SCL), J2.3, J7.4, R5.1, RN3.1
/I2C_SCL1: J2.5, J7.6, R7.1, RN3.3 (1), U1.26 (SCL)
/I2C_SCL2: J2.7, J7.8, R9.1, RN4.1
/I2C_SCL3: J2.9, J7.10, R11.1, RN4.3 (1)
/I2C_SDA0: IC5.15 (SDA), J2.4, J7.3, R6.1, RN3.2 (1)
/I2C_SDA1: J2.6, J7.5, R8.1, RN3.4 (1), U1.27 (SDA)
/I2C_SDA2: J2.8, J7.7, R10.1, RN4.2 (1)
/I2C_SDA3: J2.10, J7.9, R12.1, RN4.4 (1)
/P0: IC1.3 (P0), RN1.8 (2)
/P1: IC1.4 (P1), RN1.7 (2)
/P2: IC1.6 (P2), RN1.6 (2)
/P3: IC1.7 (P3), RN1.5 (2)
/P4: IC1.9 (P4), RN2.8 (2)
/P5: IC1.10 (P5), RN2.7 (2)
/P6: IC1.12 (P6), RN2.6 (2)
/P7: IC1.13 (P7), RN2.5 (2)
/P8: IC1.15 (P8), RN7.8 (2)
/P9: IC1.16 (P9), RN7.7 (2)
/P10: IC1.18 (P10), RN7.6 (2)
/P11: IC1.19 (P11), RN7.5 (2)
/P12: IC1.21 (P12), RN8.8 (2)
/P13: IC1.22 (P13), RN8.7 (2)
/P14: IC1.24 (P14), RN8.6 (2)
/P15: IC1.25 (P15), RN8.5 (2)
/P16: IC1.27 (P16), RN3.8 (2)
/P17: IC1.28 (P17), RN3.7 (2)
/P18: IC1.30 (P18), RN3.6 (2)
/P19: IC1.31 (P19), RN3.5 (2)
/P20: IC1.33 (P20), RN4.8 (2)
/P21: IC1.34 (P21), RN4.7 (2)
/P22: IC1.36 (P22), RN4.6 (2)
/P23: IC1.37 (P23), RN4.5 (2)
/P24: IC1.39 (P24), RN5.8 (2)
/P25: IC1.40 (P25), RN5.7 (2)
/P26: IC1.42 (P26), RN5.6 (2)
/P27: IC1.43 (P27), RN5.5 (2)
/P28: IC1.45 (P28), RN6.8 (2)
/P29: IC1.46 (P29), RN6.7 (2)
/P30: IC1.48 (P30), RN6.6 (2)
/P31: IC1.49 (P31), RN6.5 (2)
/P32: IC1.53 (P32), RN9.8 (2)
/P33: IC1.54 (P33), RN9.7 (2)
/P34: IC1.56 (P34), RN9.6 (2)
/P35: IC1.57 (P35), RN9.5 (2)
/P36: IC1.59 (P36), RN10.8 (2)
/P37: IC1.60 (P37), RN10.7 (2)
/P38: IC1.62 (P38), RN10.6 (2)
/P39: IC1.63 (P39), RN10.5 (2)
/P40: IC1.65 (P40), IC3.D3 (DQ0), IC4.D3 (DQ0)
/P41: IC1.66 (P41), IC3.D2 (DQ1), IC4.D2 (DQ1)
/P42: IC1.68 (P42), IC3.C4 (DQ2), IC4.C4 (DQ2)
/P43: IC1.69 (P43), IC3.D4 (DQ3), IC4.D4 (DQ3)
/P44: IC1.71 (P44), IC3.D5 (DQ4), IC4.D5 (DQ4)
/P45: IC1.72 (P45), IC3.E3 (DQ5), IC4.E3 (DQ5)
/P46: IC1.74 (P46), IC3.E2 (DQ6), IC4.E2 (DQ6)
/P47: IC1.75 (P47), IC3.E1 (DQ7), IC4.E1 (DQ7)
/P48: IC1.77 (P48), IC3.B2 (CK)
/P49: IC1.78 (P49), IC4.B2 (CK)
/P50: IC1.80 (P50), IC3.C3 (RWDS)
/P51: IC1.81 (P51), IC4.C3 (RWDS)
/P52: IC1.83 (P52), R17.1, R18.1
/P53: IC1.84 (P53), R19.1, R20.1
/P54: IC1.86 (P54), R21.1, R22.1
/P55: IC1.87 (P55), IC3.A4 (RESET#), IC4.A4 (RESET#)
/P56: IC1.89 (P56), RN16.8 (2)
/P57: IC1.90 (P57), RN16.7 (2)
/P58: IC1.92 (P58), RN16.6 (2)
/P59: IC1.93 (P59), RN16.5 (2)
/P60: IC1.95 (P60), RN15.8 (2)
/P61: IC1.96 (P61), RN15.7 (2)
/P62: IC1.98 (P62), RN15.6 (2)
/P63: IC1.99 (P63), RN15.5 (2)
/PWM0: J3.11, J8.12, U1.6 (PWM0)
/PWM1: J3.12, J8.11, U1.7 (PWM1)
/PWM2: J3.13, J8.14, U1.8 (PWM2)
/PWM3: J3.14, J8.13, U1.9 (PWM3)
/PWM4: J3.15, J8.16, U1.10 (PWM4)
/PWM5: J3.16, J8.15, U1.11 (PWM5)
/PWM6: J3.17, J8.18, U1.12 (PWM6)
/PWM7: J3.18, J8.17, U1.13 (PWM7)
/PWM8: J13.3, U1.15 (PWM8)
/PWM9: J13.6, U1.16 (PWM9)
/PWM10: J13.9, U1.17 (PWM10)
/PWM11: J13.12, U1.18 (PWM11)
/PWM12: J13.15, U1.19 (PWM12)
/PWM13: J13.18, U1.20 (PWM13)
/PWM14: J13.21, U1.21 (PWM14)
/PWM15: J13.24, U1.22 (PWM15)
/RAM_A_CS: IC3.A3 (CS#_DNU), R18.2
/RAM_B_CS: IC4.A3 (CS#_DNU), R20.2
/RESET_N: IC1.100 (RESN), J4.18, J6.3, J9.17, J11.2, R16.1
/RTC_SCL: R13.1, RN16.1, U$3.8 (SCL)
/RTC_SDA: R14.1, RN16.2 (1), U$3.7 (SDA)
/RXD: J4.19, J6.2, J9.20, RN15.4 (1)
/SD_CLK: J11.3, RN15.2 (1), U$2.5 (SCLK)
/SPI_MISO0: J1.5, J5.6, RN1.3 (1)
/SPI_MISO1: J1.9, J5.10, RN2.3 (1)
/SPI_MISO2: J1.13, J5.14, RN7.3 (1)
/SPI_MISO3: J1.17, J5.18, RN8.3 (1)
/SPI_MOSI0: J1.4, J5.3, RN1.2 (1)
/SPI_MOSI1: J1.8, J5.7, RN2.2 (1)
/SPI_MOSI2: J1.12, J5.11, RN7.2 (1)
/SPI_MOSI3: J1.16, J5.15, RN8.2 (1)
/SPI_SCLK0: J1.3, J5.4, RN1.1
/SPI_SCLK1: J1.7, J5.8, RN2.1
/SPI_SCLK2: J1.11, J5.12, RN7.1
/SPI_SCLK3: J1.15, J5.16, RN8.1
/SPI_SS0: J1.6, J5.5, RN1.4 (1)
/SPI_SS1: J1.10, J5.9, RN2.4 (1)
/SPI_SS2: J1.14, J5.13, RN7.4 (1)
/SPI_SS3: J1.18, J5.17, RN8.4 (1)
/TXD: J4.20, J6.1, J9.19, RN15.3 (1)
/UART_RX0: J2.11, J7.12, RN5.1
/UART_RX1: J2.13, J7.14, RN5.3 (1)
/UART_RX2: J2.15, J7.16, RN6.1
/UART_RX3: J2.17, J7.18, RN6.3 (1)
/UART_TX0: J2.12, J7.11, RN5.2 (1)
/UART_TX1: J2.14, J7.13, RN5.4 (1)
/UART_TX2: J2.16, J7.15, RN6.2 (1)
/UART_TX3: J2.18, J7.17, RN6.4 (1)
GND: C1.2, C2.2, C3.2, C4.2, C5.2, C6.2, C7.2, C8.2, C9.2, C10.2, C11.2, C12.2, C13.2, C14.2, C15.-, C16.2, C17.2, C18.2, C19.2, IC1.1 (TEST), IC1.EPAD (GND), IC2.4 (GND), IC3.B3 (VSS), IC3.C1 (VSSQ@1), IC3.E5 (VSSQ@2), IC4.B3 (VSS), IC4.C1 (VSSQ@1), IC4.E5 (VSSQ@2), IC5.1 (A0), IC5.2 (A1), IC5.3 (A2), IC5.8 (VSS), J1.1, J1.2, J1.19, J1.20, J2.1, J2.2, J2.19, J2.20, J3.1, J3.2, J3.19, J3.20, J4.1, J4.2, J4.3, J4.4, J5.1, J5.2, J5.19, J5.20, J6.4, J7.1, J7.2, J7.19, J7.20, J8.1, J8.2, J8.19, J8.20, J9.1, J9.2, J9.3, J9.4, J12.9, J13.1, J13.4, J13.7, J13.10, J13.13, J13.16, J13.19, J13.22, R2.2, U1.1 (A0), U1.2 (A1), U1.3 (A2), U1.4 (A3), U1.5 (A4), U1.14 (GND), U1.23 (#OE), U1.24 (A5), U1.25 (EXTCLK), U$2.6 (GND), U$3.5 (GND)
unnamed: C15.+, R15.2
unnamed: D1.C, R15.1, U$3.6 (VBAT)
unnamed: IC1.50 (XO), Y1.P$1 (1)
unnamed: IC1.51 (XI), Y1.P$2 (2)
unnamed: IC2.1 (CS), J11.4, R1.1
unnamed: J11.5, R3.1
unnamed: J11.7, R2.1
unnamed: R4.2, U$2.7 (DOUT)
U_1V8: C1.1, C2.1, C3.1, C4.1, C5.1, C6.1, C7.1, C8.1, IC1.2 (VDD@1), IC1.8 (VDD@2), IC1.14 (VDD@3), IC1.20 (VDD@4), IC1.26 (VDD@5), IC1.32 (VDD@6), IC1.38 (VDD@7), IC1.44 (VDD@8), IC1.52 (VDD@9), IC1.58 (VDD@10), IC1.64 (VDD@11), IC1.70 (VDD@12), IC1.76 (VDD@13), IC1.82 (VDD@14), IC1.88 (VDD@15), IC1.94 (VDD@16), J4.5, J4.6, J4.7, J4.8, J9.5, J9.6, J9.7, J9.8
U_3V3: C9.1, C10.1, C11.1, C12.1, C13.1, C14.1, C16.1, C18.1, C19.1, D1.A, IC1.5 (V0003), IC1.11 (V0407), IC1.17 (V0811), IC1.23 (V1215), IC1.29 (V1619), IC1.35 (V2023), IC1.41 (V2427), IC1.47 (V2831), IC1.55 (V3235), IC1.61 (V3639), IC1.67 (V4043), IC1.73 (V4447), IC1.79 (V4851), IC1.85 (V5255), IC1.91 (V5659), IC1.97 (V6063), IC2.3 (WP), IC2.7 (HOLD), IC2.8 (VCC), IC3.B4 (VCC), IC3.D1 (VCCQ@1), IC3.E4 (VCCQ@2), IC4.B4 (VCC), IC4.D1 (VCCQ@1), IC4.E4 (VCCQ@2), IC5.16 (VDD), J4.9, J4.10, J4.11, J4.12, J9.9, J9.10, J9.11, J9.12, J12.10, R1.2, R3.2, R5.2, R6.2, R7.2, R8.2, R9.2, R10.2, R11.2, R12.2, R13.2, R14.2, R16.2, U$2.4 (VDD), U$3.2 (VCC)
U_5V: C17.1, J4.13, J4.14, J4.15, J4.16, J9.13, J9.14, J9.15, J9.16, J13.2, J13.5, J13.8, J13.11, J13.14, J13.17, J13.20, J13.23, U1.28 (VDD)

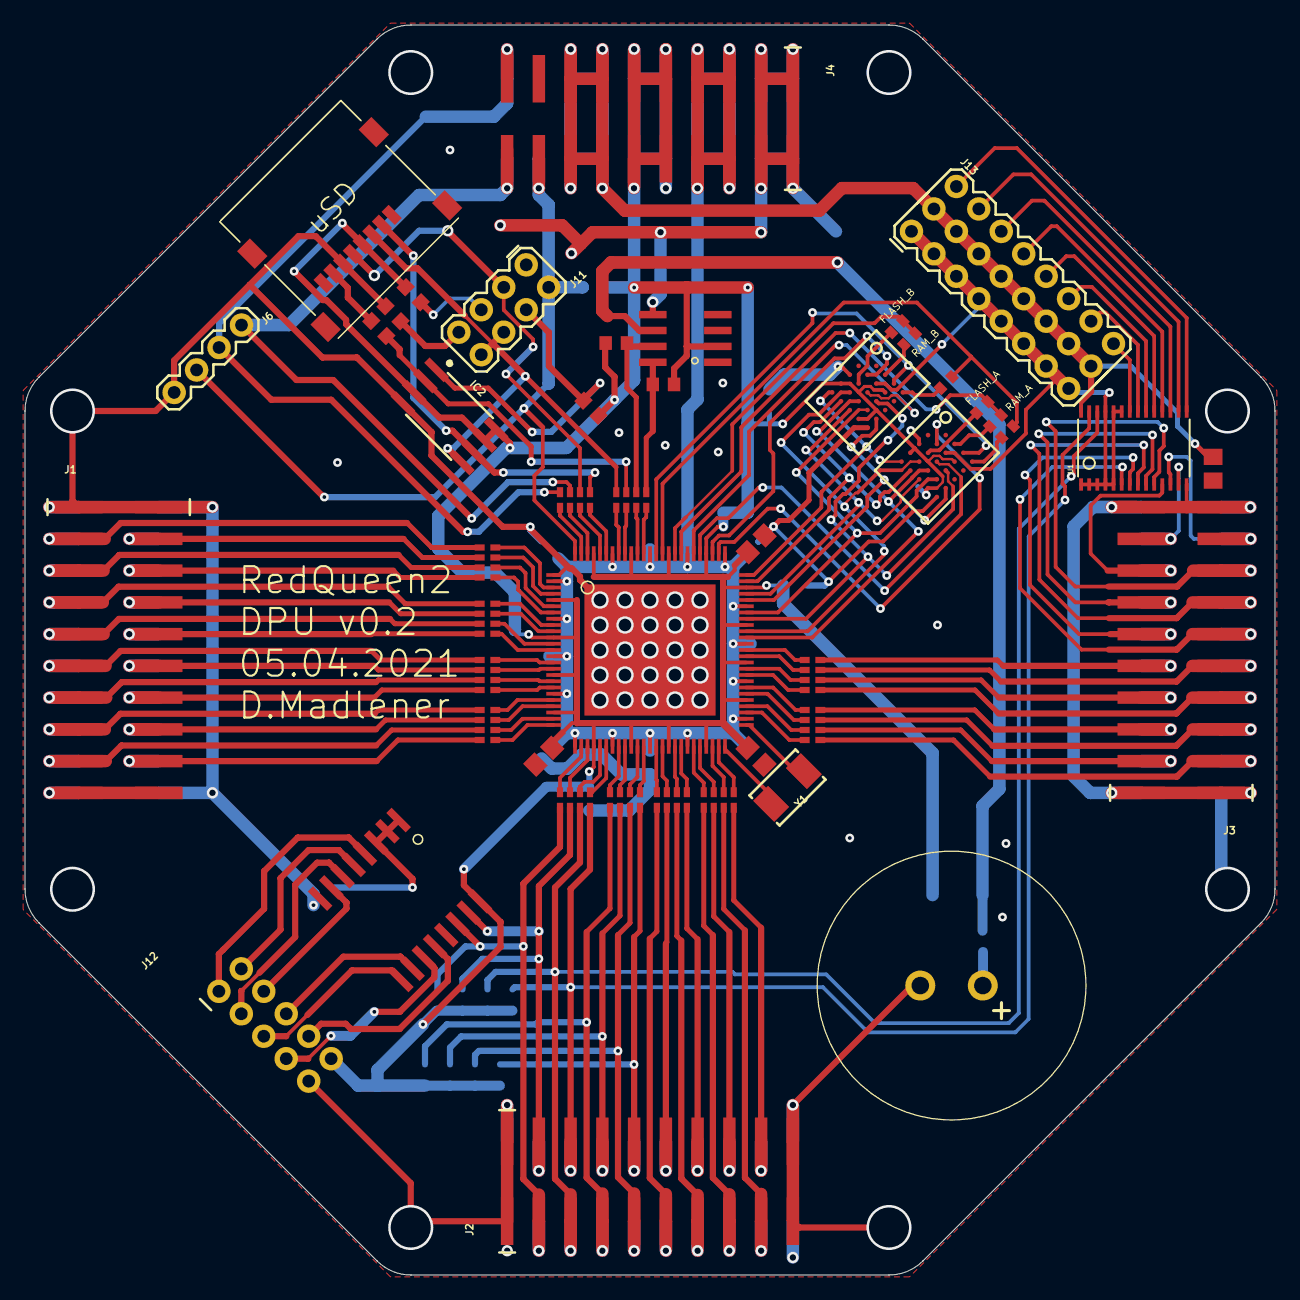
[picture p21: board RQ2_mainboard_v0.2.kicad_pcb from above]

Board: 2 copper layers, 100.0 x 100.0 mm, 75 parts (0 on the bottom side), 155 nets.

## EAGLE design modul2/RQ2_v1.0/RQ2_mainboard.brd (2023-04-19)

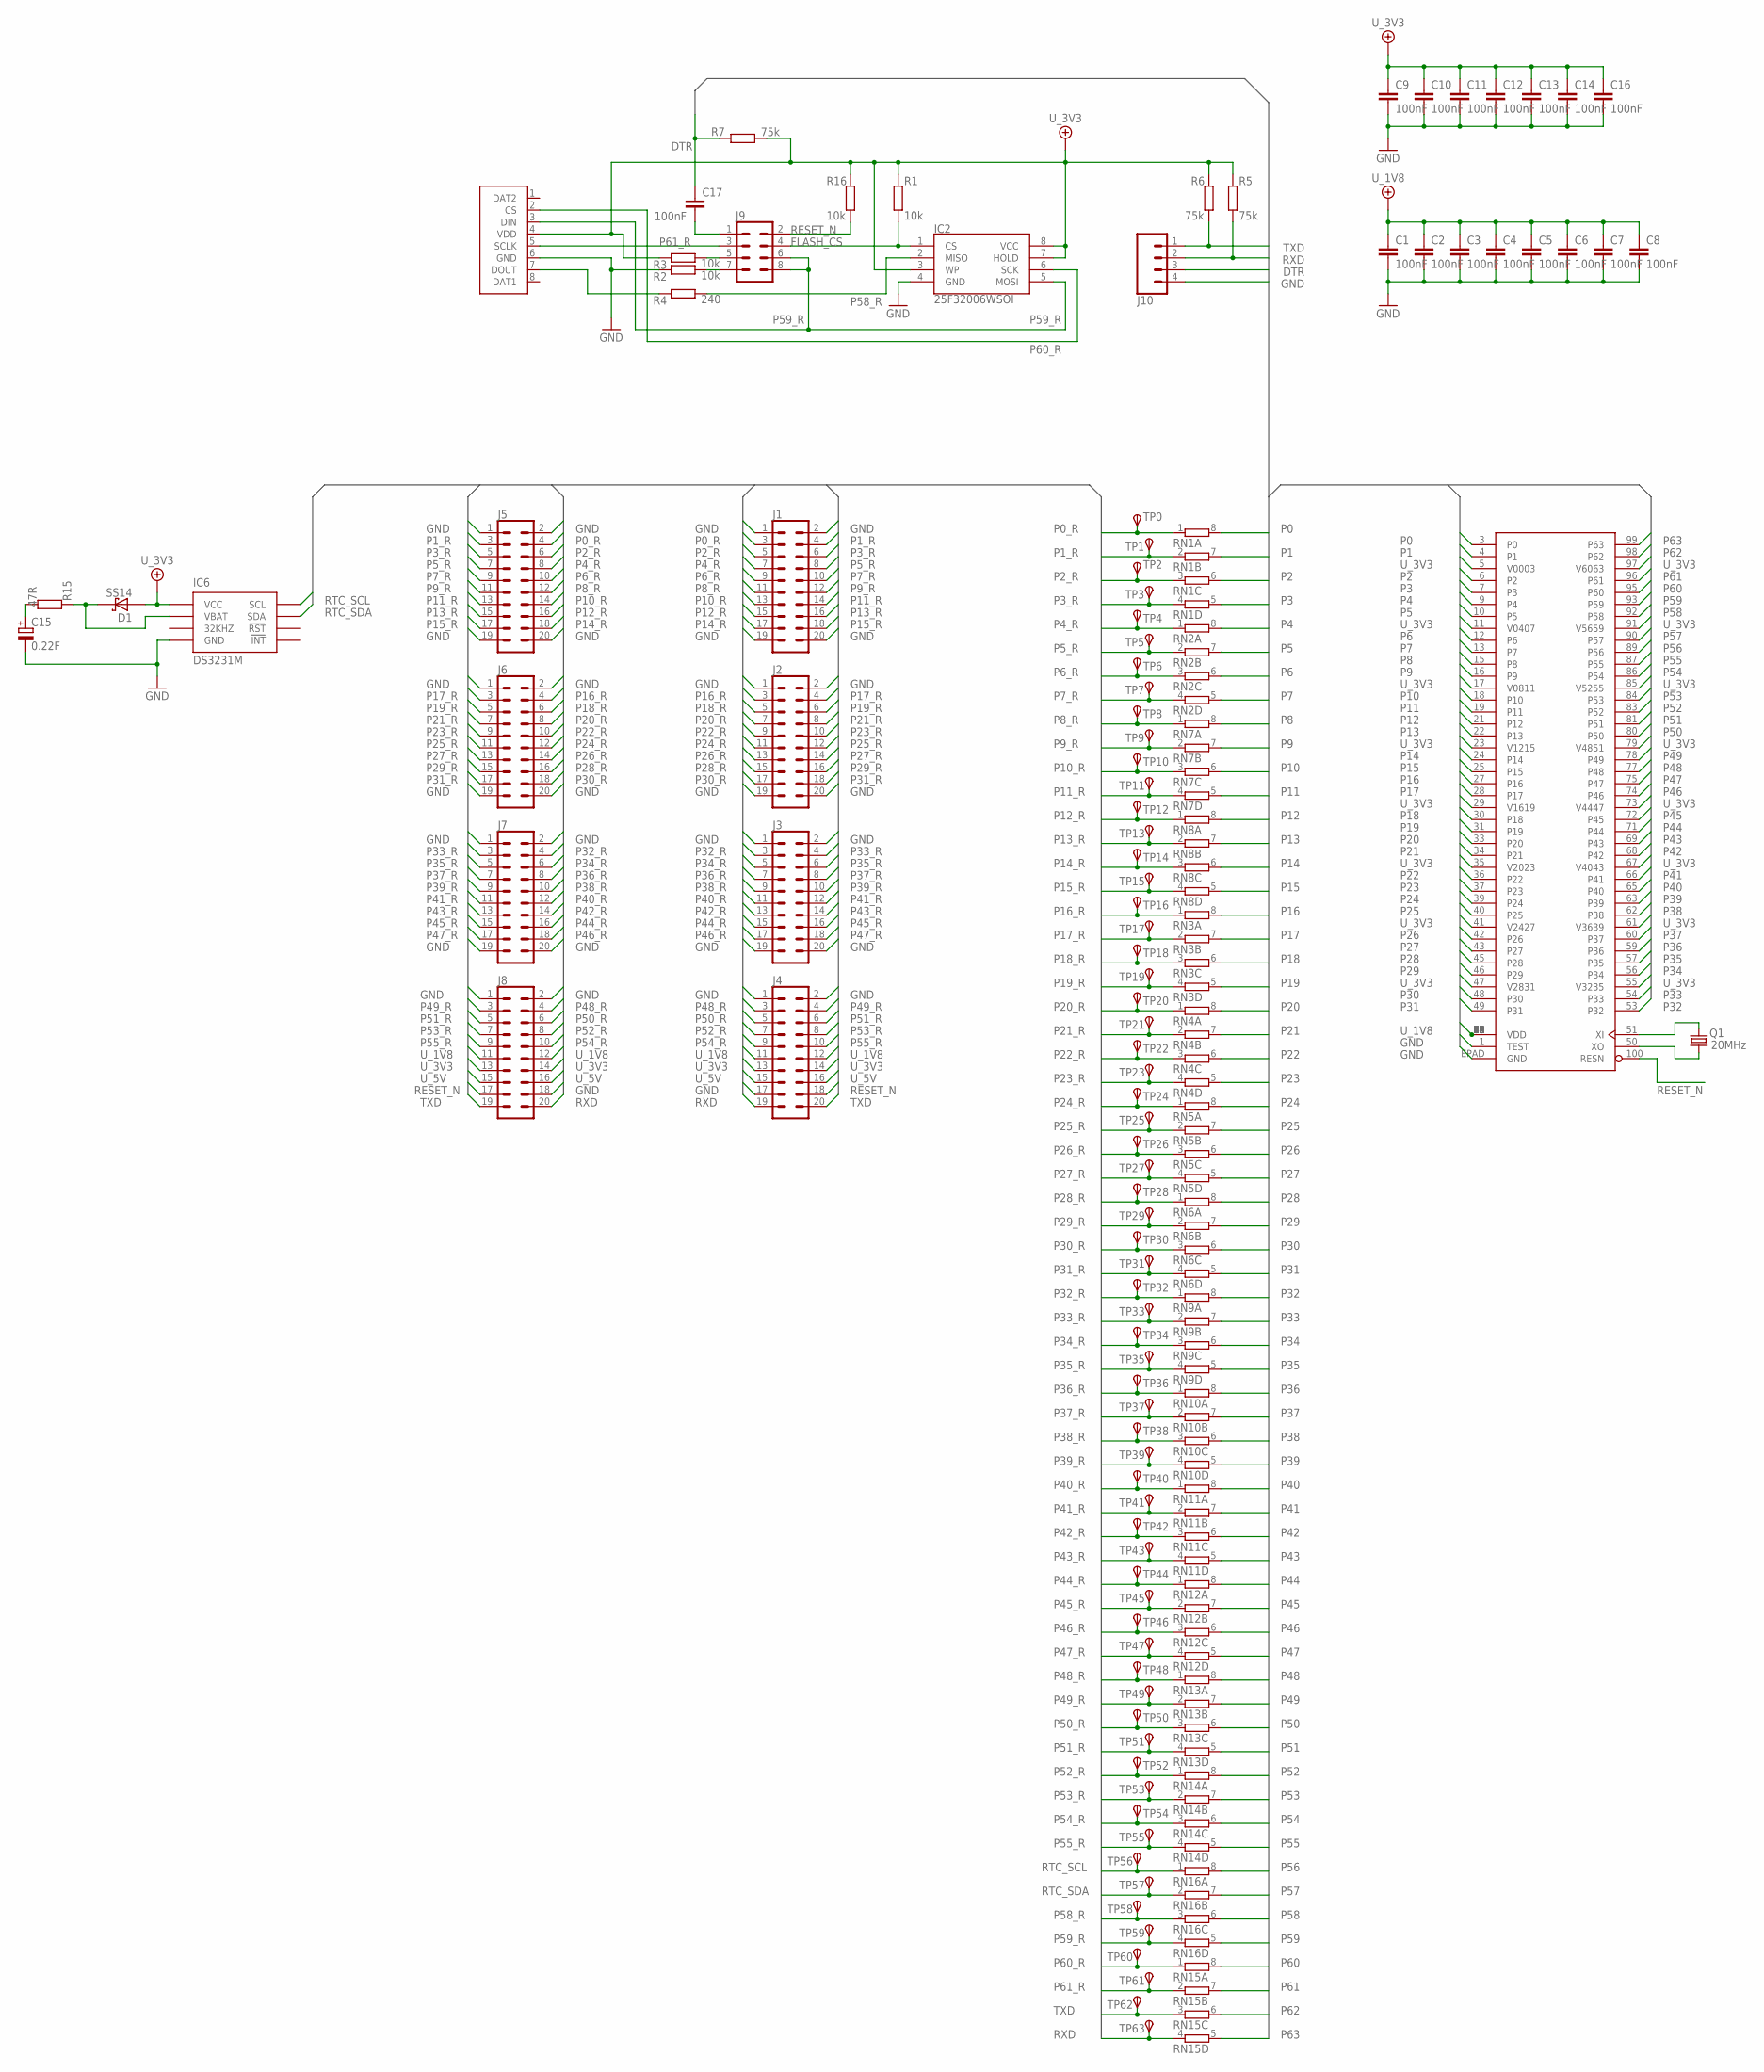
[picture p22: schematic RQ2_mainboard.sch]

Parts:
C1, C2, C3, C4, C5, C6, C7, C8, C9, C10, C11, C12, C13, C14, C16, C17: 100nF; C0805
C15: 0.22F; DHL_21.5
D1: SS14; SMA_403D
IC1: P2X8C4M64P; TQFP100
IC2: 25F32006WSOI; SO08-EIAJ
IC6: DS3231M; SO-8
J1, J2, J3, J4, J5, J6, J7, J8: CONN_10X2SMT; 2X10_SMT
J9: CONN_04X2; 2X4
J10: CONN_04; 1X04
Q1: 20MHz; CRYSTAL-SMD-5X3.2-2PAD
R1, R2, R3, R16: 10k; R0603
R4: 240; R0603
R5, R6, R7: 75k; R0603
R15: 47R; R0603
RN1, RN2, RN3, RN4, RN5, RN6, RN7, RN8, RN9, RN10, RN11, RN12, RN13, RN14, RN15, RN16: 4R-N0603-ARV; 0603-ARV
TP0, TP1, TP2, TP3, TP4, TP5, TP6, TP7, TP8, TP9, TP10, TP11, TP12, TP13, TP14, TP15, TP16, TP17, TP18, TP19, TP20, TP21, TP22, TP23, TP24, TP25, TP26, TP27, TP28, TP29, TP30, TP31, TP32, TP33, TP34, TP35, TP36, TP37, TP38, TP39, TP40, TP41, TP42, TP43, TP44, TP45, TP46, TP47, TP48, TP49, TP50, TP51, TP52, TP53, TP54, TP55, TP56, TP57, TP58, TP59, TP60, TP61, TP62, TP63: TPSB1,27; B1,27
X1: MICRO_SD_CONNECTORMOLEX_HINGE; MICRO_SD

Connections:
DTR: C17.1, J10.3, R7.2
DTR_C: C17.2, J9.1
FLASH_CS: IC2.1 (CS), J9.4, R1.1
GND: C1.2, C2.2, C3.2, C4.2, C5.2, C6.2, C7.2, C8.2, C9.2, C10.2, C11.2, C12.2, C13.2, C14.2, C15.-, C16.2, IC1.1 (TEST), IC1.EPAD (GND), IC2.4 (GND), IC6.5 (GND), J1.1, J1.2, J1.19, J1.20, J2.1, J2.2, J2.19, J2.20, J3.1, J3.2, J3.19, J3.20, J4.1, J4.2, J4.17, J5.1, J5.2, J5.19, J5.20, J6.1, J6.2, J6.19, J6.20, J7.1, J7.2, J7.19, J7.20, J8.1, J8.2, J8.18, J10.4, R2.2, X1.6 (GND)
unnamed: J9.7, R2.1
unnamed: J9.5, R3.1
P0: IC1.3 (P0), RN1.8 (2)
P0_R: J1.3, J5.4, RN1.1, TP0.TP
P1: IC1.4 (P1), RN1.7 (2)
P1_R: J1.4, J5.3, RN1.2 (1), TP1.TP
P2: IC1.6 (P2), RN1.6 (2)
P2_R: J1.5, J5.6, RN1.3 (1), TP2.TP
P3: IC1.7 (P3), RN1.5 (2)
P3_R: J1.6, J5.5, RN1.4 (1), TP3.TP
P4: IC1.9 (P4), RN2.8 (2)
P4_R: J1.7, J5.8, RN2.1, TP4.TP
P5: IC1.10 (P5), RN2.7 (2)
P5_R: J1.8, J5.7, RN2.2 (1), TP5.TP
P6: IC1.12 (P6), RN2.6 (2)
P6_R: J1.9, J5.10, RN2.3 (1), TP6.TP
P7: IC1.13 (P7), RN2.5 (2)
P7_R: J1.10, J5.9, RN2.4 (1), TP7.TP
P8: IC1.15 (P8), RN7.8 (2)
P8_R: J1.11, J5.12, RN7.1, TP8.TP
P9: IC1.16 (P9), RN7.7 (2)
P9_R: J1.12, J5.11, RN7.2 (1), TP9.TP
P10: IC1.18 (P10), RN7.6 (2)
P10_R: J1.13, J5.14, RN7.3 (1), TP10.TP
P11: IC1.19 (P11), RN7.5 (2)
P11_R: J1.14, J5.13, RN7.4 (1), TP11.TP
P12: IC1.21 (P12), RN8.8 (2)
P12_R: J1.15, J5.16, RN8.1, TP12.TP
P13: IC1.22 (P13), RN8.7 (2)
P13_R: J1.16, J5.15, RN8.2 (1), TP13.TP
P14: IC1.24 (P14), RN8.6 (2)
P14_R: J1.17, J5.18, RN8.3 (1), TP14.TP
P15: IC1.25 (P15), RN8.5 (2)
P15_R: J1.18, J5.17, RN8.4 (1), TP15.TP
P16: IC1.27 (P16), RN3.8 (2)
P16_R: J2.3, J6.4, RN3.1, TP16.TP
P17: IC1.28 (P17), RN3.7 (2)
P17_R: J2.4, J6.3, RN3.2 (1), TP17.TP
P18: IC1.30 (P18), RN3.6 (2)
P18_R: J2.5, J6.6, RN3.3 (1), TP18.TP
P19: IC1.31 (P19), RN3.5 (2)
P19_R: J2.6, J6.5, RN3.4 (1), TP19.TP
P20: IC1.33 (P20), RN4.8 (2)
P20_R: J2.7, J6.8, RN4.1, TP20.TP
P21: IC1.34 (P21), RN4.7 (2)
P21_R: J2.8, J6.7, RN4.2 (1), TP21.TP
P22: IC1.36 (P22), RN4.6 (2)
P22_R: J2.9, J6.10, RN4.3 (1), TP22.TP
P23: IC1.37 (P23), RN4.5 (2)
P23_R: J2.10, J6.9, RN4.4 (1), TP23.TP
P24: IC1.39 (P24), RN5.8 (2)
P24_R: J2.11, J6.12, RN5.1, TP24.TP
P25: IC1.40 (P25), RN5.7 (2)
P25_R: J2.12, J6.11, RN5.2 (1), TP25.TP
P26: IC1.42 (P26), RN5.6 (2)
P26_R: J2.13, J6.14, RN5.3 (1), TP26.TP
P27: IC1.43 (P27), RN5.5 (2)
P27_R: J2.14, J6.13, RN5.4 (1), TP27.TP
P28: IC1.45 (P28), RN6.8 (2)
P28_R: J2.15, J6.16, RN6.1, TP28.TP
P29: IC1.46 (P29), RN6.7 (2)
P29_R: J2.16, J6.15, RN6.2 (1), TP29.TP
P30: IC1.48 (P30), RN6.6 (2)
P30_R: J2.17, J6.18, RN6.3 (1), TP30.TP
P31: IC1.49 (P31), RN6.5 (2)
P31_R: J2.18, J6.17, RN6.4 (1), TP31.TP
P32: IC1.53 (P32), RN9.8 (2)
P32_R: J3.3, J7.4, RN9.1, TP32.TP
P33: IC1.54 (P33), RN9.7 (2)
P33_R: J3.4, J7.3, RN9.2 (1), TP33.TP
P34: IC1.56 (P34), RN9.6 (2)
P34_R: J3.5, J7.6, RN9.3 (1), TP34.TP
P35: IC1.57 (P35), RN9.5 (2)
P35_R: J3.6, J7.5, RN9.4 (1), TP35.TP
P36: IC1.59 (P36), RN10.8 (2)
P36_R: J3.7, J7.8, RN10.1, TP36.TP
P37: IC1.60 (P37), RN10.7 (2)
P37_R: J3.8, J7.7, RN10.2 (1), TP37.TP
P38: IC1.62 (P38), RN10.6 (2)
P38_R: J3.9, J7.10, RN10.3 (1), TP38.TP
P39: IC1.63 (P39), RN10.5 (2)
P39_R: J3.10, J7.9, RN10.4 (1), TP39.TP
P40: IC1.65 (P40), RN11.8 (2)
P40_R: J3.11, J7.12, RN11.1, TP40.TP
P41: IC1.66 (P41), RN11.7 (2)
P41_R: J3.12, J7.11, RN11.2 (1), TP41.TP
P42: IC1.68 (P42), RN11.6 (2)
P42_R: J3.13, J7.14, RN11.3 (1), TP42.TP
P43: IC1.69 (P43), RN11.5 (2)
P43_R: J3.14, J7.13, RN11.4 (1), TP43.TP
P44: IC1.71 (P44), RN12.8 (2)
P44_R: J3.15, J7.16, RN12.1, TP44.TP
P45: IC1.72 (P45), RN12.7 (2)
P45_R: J3.16, J7.15, RN12.2 (1), TP45.TP
P46: IC1.74 (P46), RN12.6 (2)
P46_R: J3.17, J7.18, RN12.3 (1), TP46.TP
P47: IC1.75 (P47), RN12.5 (2)
P47_R: J3.18, J7.17, RN12.4 (1), TP47.TP
P48: IC1.77 (P48), RN13.8 (2)
P48_R: J4.3, J8.4, RN13.1, TP48.TP
P49: IC1.78 (P49), RN13.7 (2)
P49_R: J4.4, J8.3, RN13.2 (1), TP49.TP
P50: IC1.80 (P50), RN13.6 (2)
P50_R: J4.5, J8.6, RN13.3 (1), TP50.TP
P51: IC1.81 (P51), RN13.5 (2)
P51_R: J4.6, J8.5, RN13.4 (1), TP51.TP
P52: IC1.83 (P52), RN14.8 (2)
P52_R: J4.7, J8.8, RN14.1, TP52.TP
P53: IC1.84 (P53), RN14.7 (2)
P53_R: J4.8, J8.7, RN14.2 (1), TP53.TP
P54: IC1.86 (P54), RN14.6 (2)
P54_R: J4.9, J8.10, RN14.3 (1), TP54.TP
P55: IC1.87 (P55), RN14.5 (2)
P55_R: J4.10, J8.9, RN14.4 (1), TP55.TP
P56: IC1.89 (P56), RN16.8 (2)
P57: IC1.90 (P57), RN16.7 (2)
P58: IC1.92 (P58), RN16.6 (2)
P58_R: IC2.2 (MISO), R4.1, RN16.3 (1), TP58.TP
P59: IC1.93 (P59), RN16.5 (2)
P59_R: IC2.5 (MOSI), J9.6, J9.8, RN16.4 (1), TP59.TP, X1.3 (DIN)
P60: IC1.95 (P60), RN15.8 (2)
P60_R: IC2.6 (SCK), RN15.1, TP60.TP, X1.2 (CS)
P61: IC1.96 (P61), RN15.7 (2)
P61_R: J9.3, RN15.2 (1), TP61.TP, X1.5 (SCLK)
P62: IC1.98 (P62), RN15.6 (2)
P63: IC1.99 (P63), RN15.5 (2)
RESET_N: IC1.100 (RESN), J4.18, J8.17, J9.2, R16.1
RTC_SCL: IC6.8 (SCL), RN16.1, TP56.TP
RTC_SDA: IC6.7 (SDA), RN16.2 (1), TP57.TP
RXD: J4.19, J8.20, J10.2, R5.1, RN15.4 (1), TP63.TP
SD_DOUT: R4.2, X1.7 (DOUT)
TXD: J4.20, J8.19, J10.1, R6.1, RN15.3 (1), TP62.TP
U_1V8: C1.1, C2.1, C3.1, C4.1, C5.1, C6.1, C7.1, C8.1, IC1.2 (VDD), IC1.8 (VDD), IC1.14 (VDD), IC1.20 (VDD), IC1.26 (VDD), IC1.32 (VDD), IC1.38 (VDD), IC1.44 (VDD), IC1.52 (VDD), IC1.58 (VDD), IC1.64 (VDD), IC1.70 (VDD), IC1.76 (VDD), IC1.82 (VDD), IC1.88 (VDD), IC1.94 (VDD), J4.11, J4.12, J8.11, J8.12
U_3V3: C9.1, C10.1, C11.1, C12.1, C13.1, C14.1, C16.1, D1.A, IC1.5 (V0003), IC1.11 (V0407), IC1.17 (V0811), IC1.23 (V1215), IC1.29 (V1619), IC1.35 (V2023), IC1.41 (V2427), IC1.47 (V2831), IC1.55 (V3235), IC1.61 (V3639), IC1.67 (V4043), IC1.73 (V4447), IC1.79 (V4851), IC1.85 (V5255), IC1.91 (V5659), IC1.97 (V6063), IC2.3 (WP), IC2.7 (HOLD), IC2.8 (VCC), IC6.2 (VCC), J4.13, J4.14, J8.13, J8.14, R1.2, R3.2, R5.2, R6.2, R7.1, R16.2, X1.4 (VDD)
U_5V: J4.15, J4.16, J8.15, J8.16
VBAT: D1.C, IC6.6 (VBAT), R15.1
VCAP: C15.+, R15.2
XIN: IC1.51 (XI), Q1.P$2 (2)
XOUT: IC1.50 (XO), Q1.P$1 (1)

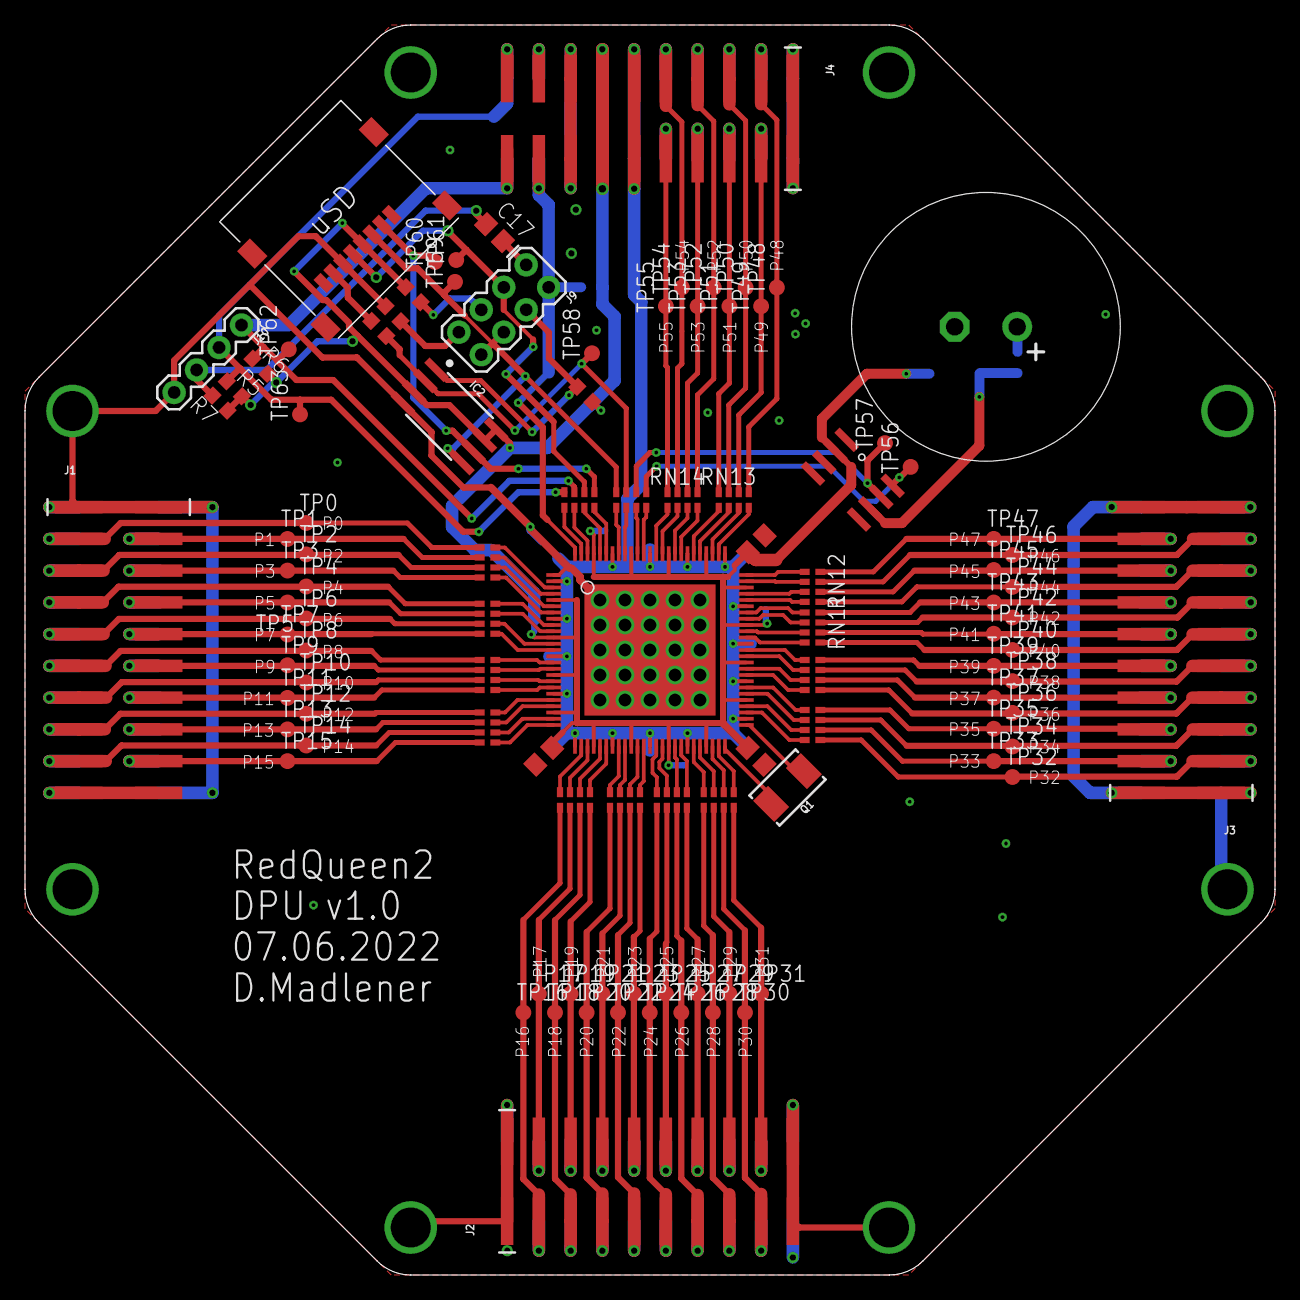
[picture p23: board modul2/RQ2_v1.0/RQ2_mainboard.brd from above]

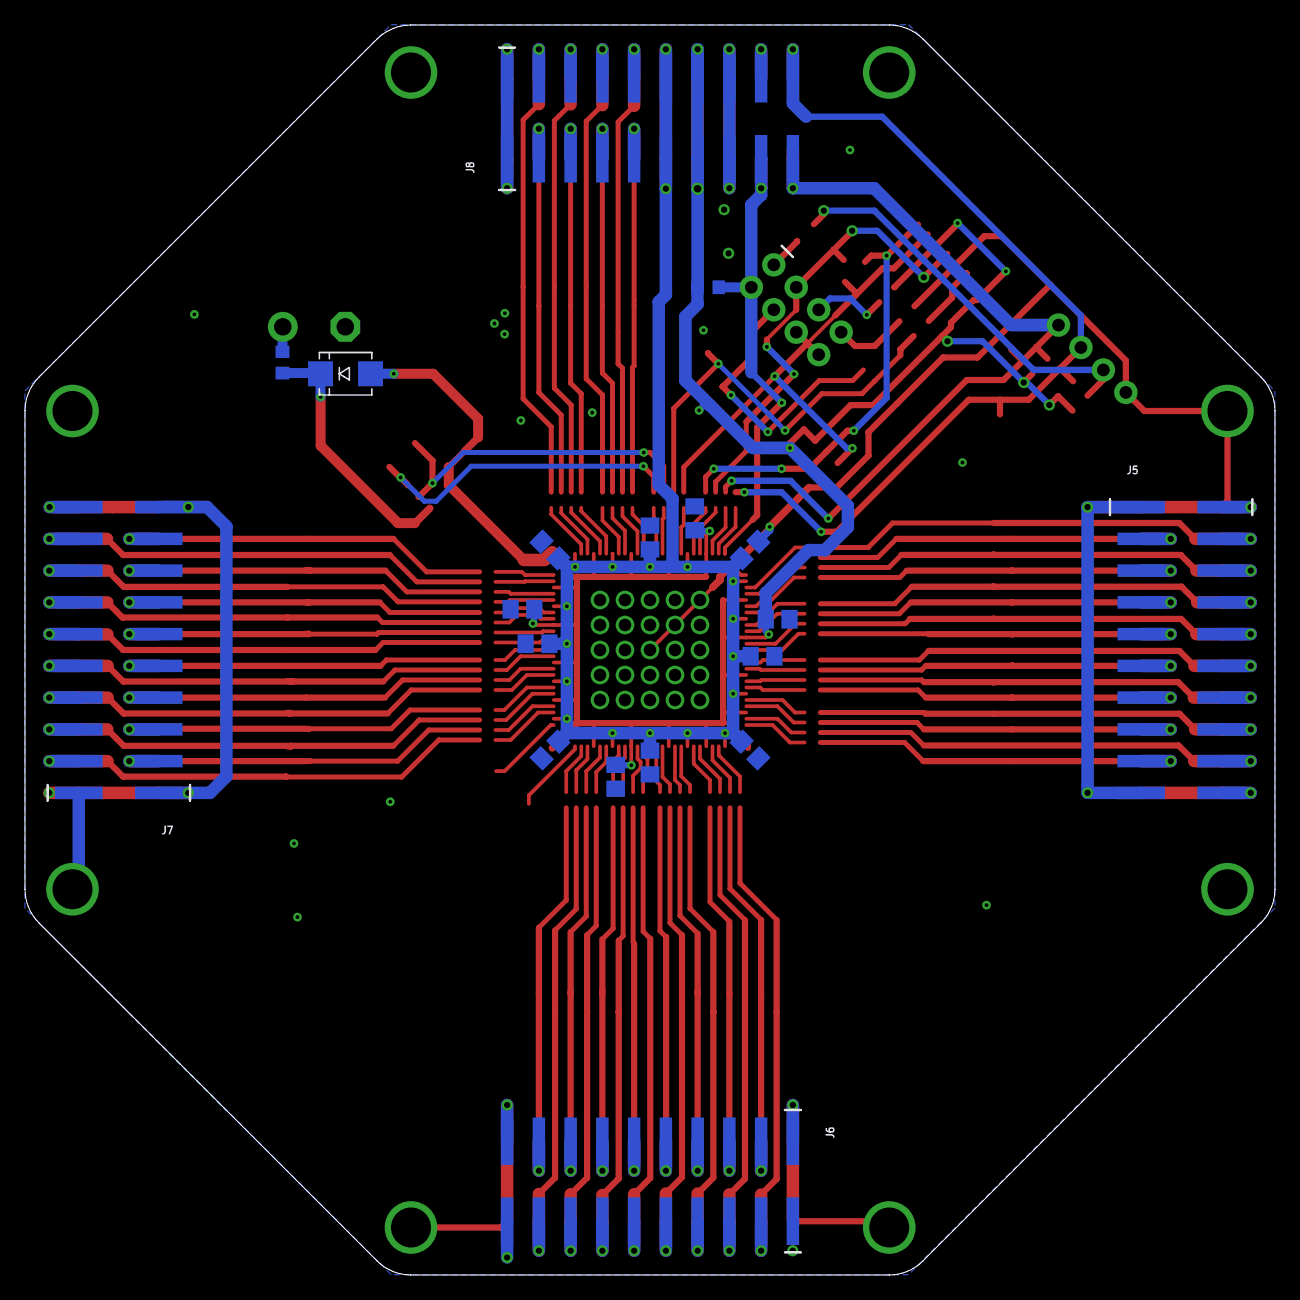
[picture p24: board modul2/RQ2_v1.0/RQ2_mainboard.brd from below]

Board: 2 copper layers, 100.0 x 100.0 mm, 122 parts (19 on the bottom side), 143 nets.

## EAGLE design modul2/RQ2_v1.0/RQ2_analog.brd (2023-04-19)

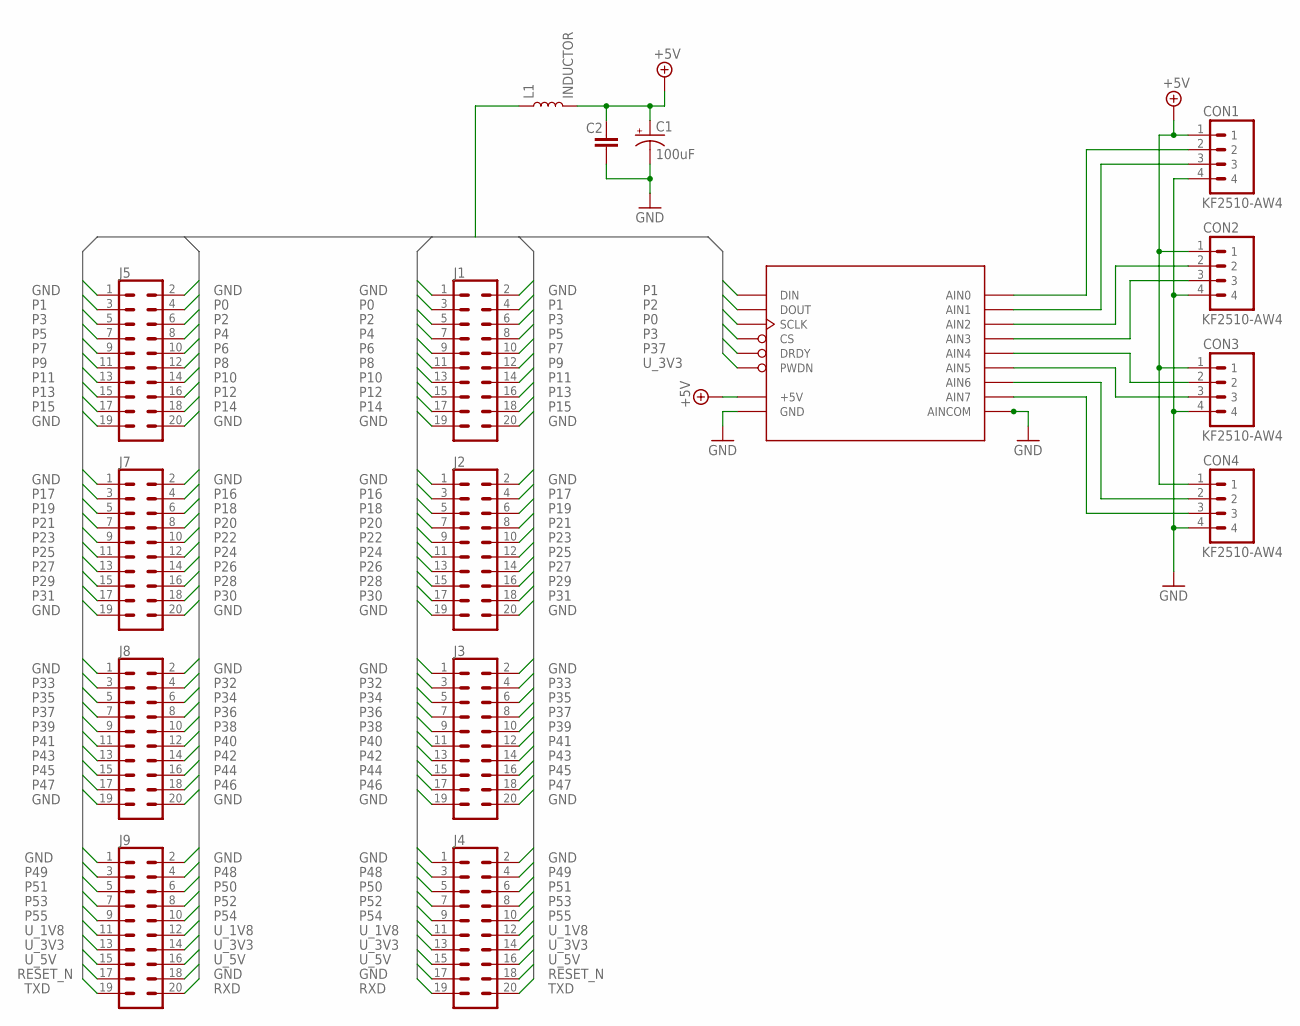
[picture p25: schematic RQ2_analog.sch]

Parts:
C1: 100uF; NIC_10X10.5_CAP
C2: 22uF; 1210
CON1, CON2, CON3, CON4: KF2510-AW4
J1, J2, J3, J4, J5, J7, J8, J9: CONN_10X2SMT; 2X10_SMT
L1: INDUCTOR; 1040
U$1: ADS1256_MODULE

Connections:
+5V: C1.+, C2.1, CON1.1, CON2.1, CON3.1, CON4.1, L1.2, U$1.+5V
GND: C1.-, C2.2, CON1.4, CON2.4, CON3.4, CON4.4, J1.1, J1.2, J1.19, J1.20, J2.1, J2.2, J2.19, J2.20, J3.1, J3.2, J3.19, J3.20, J4.1, J4.2, J4.17, J5.1, J5.2, J5.19, J5.20, J7.1, J7.2, J7.19, J7.20, J8.1, J8.2, J8.19, J8.20, J9.1, J9.2, J9.18, U$1.AINCOM0 (AINCOM), U$1.AINCOM1 (AINCOM), U$1.AINCOM2 (AINCOM), U$1.AINCOM3 (AINCOM), U$1.AINCOM4 (AINCOM), U$1.AINCOM5 (AINCOM), U$1.AINCOM6 (AINCOM), U$1.AINCOM7 (AINCOM), U$1.GND
unnamed: CON1.2, U$1.AIN0
unnamed: CON1.3, U$1.AIN1
unnamed: CON2.2, U$1.AIN2
unnamed: CON2.3, U$1.AIN3
unnamed: CON3.2, U$1.AIN4
unnamed: CON3.3, U$1.AIN5
unnamed: CON4.2, U$1.AIN6
unnamed: CON4.3, U$1.AIN7
P0: J1.3, J5.4, U$1.SCLK
P1: J1.4, J5.3, U$1.DIN
P2: J1.5, J5.6, U$1.DOUT
P3: J1.6, J5.5, U$1.CS
P4: J1.7, J5.8
P5: J1.8, J5.7
P6: J1.9, J5.10
P7: J1.10, J5.9
P8: J1.11, J5.12
P9: J1.12, J5.11
P10: J1.13, J5.14
P11: J1.14, J5.13
P12: J1.15, J5.16
P13: J1.16, J5.15
P14: J1.17, J5.18
P15: J1.18, J5.17
P16: J2.3, J7.4
P17: J2.4, J7.3
P18: J2.5, J7.6
P19: J2.6, J7.5
P20: J2.7, J7.8
P21: J2.8, J7.7
P22: J2.9, J7.10
P23: J2.10, J7.9
P24: J2.11, J7.12
P25: J2.12, J7.11
P26: J2.13, J7.14
P27: J2.14, J7.13
P28: J2.15, J7.16
P29: J2.16, J7.15
P30: J2.17, J7.18
P31: J2.18, J7.17
P32: J3.3, J8.4
P33: J3.4, J8.3
P34: J3.5, J8.6
P35: J3.6, J8.5
P36: J3.7, J8.8
P37: J3.8, J8.7, U$1.DRDY
P38: J3.9, J8.10
P39: J3.10, J8.9
P40: J3.11, J8.12
P41: J3.12, J8.11
P42: J3.13, J8.14
P43: J3.14, J8.13
P44: J3.15, J8.16
P45: J3.16, J8.15
P46: J3.17, J8.18
P47: J3.18, J8.17
P48: J4.3, J9.4
P49: J4.4, J9.3
P50: J4.5, J9.6
P51: J4.6, J9.5
P52: J4.7, J9.8
P53: J4.8, J9.7
P54: J4.9, J9.10
P55: J4.10, J9.9
RESET_N: J4.18, J9.17
RXD: J4.19, J9.20
TXD: J4.20, J9.19
U_1V8: J4.11, J4.12, J9.11, J9.12
U_3V3: J4.13, J4.14, J9.13, J9.14, U$1.PWDN
U_5V: J4.15, J4.16, J9.15, J9.16, L1.1

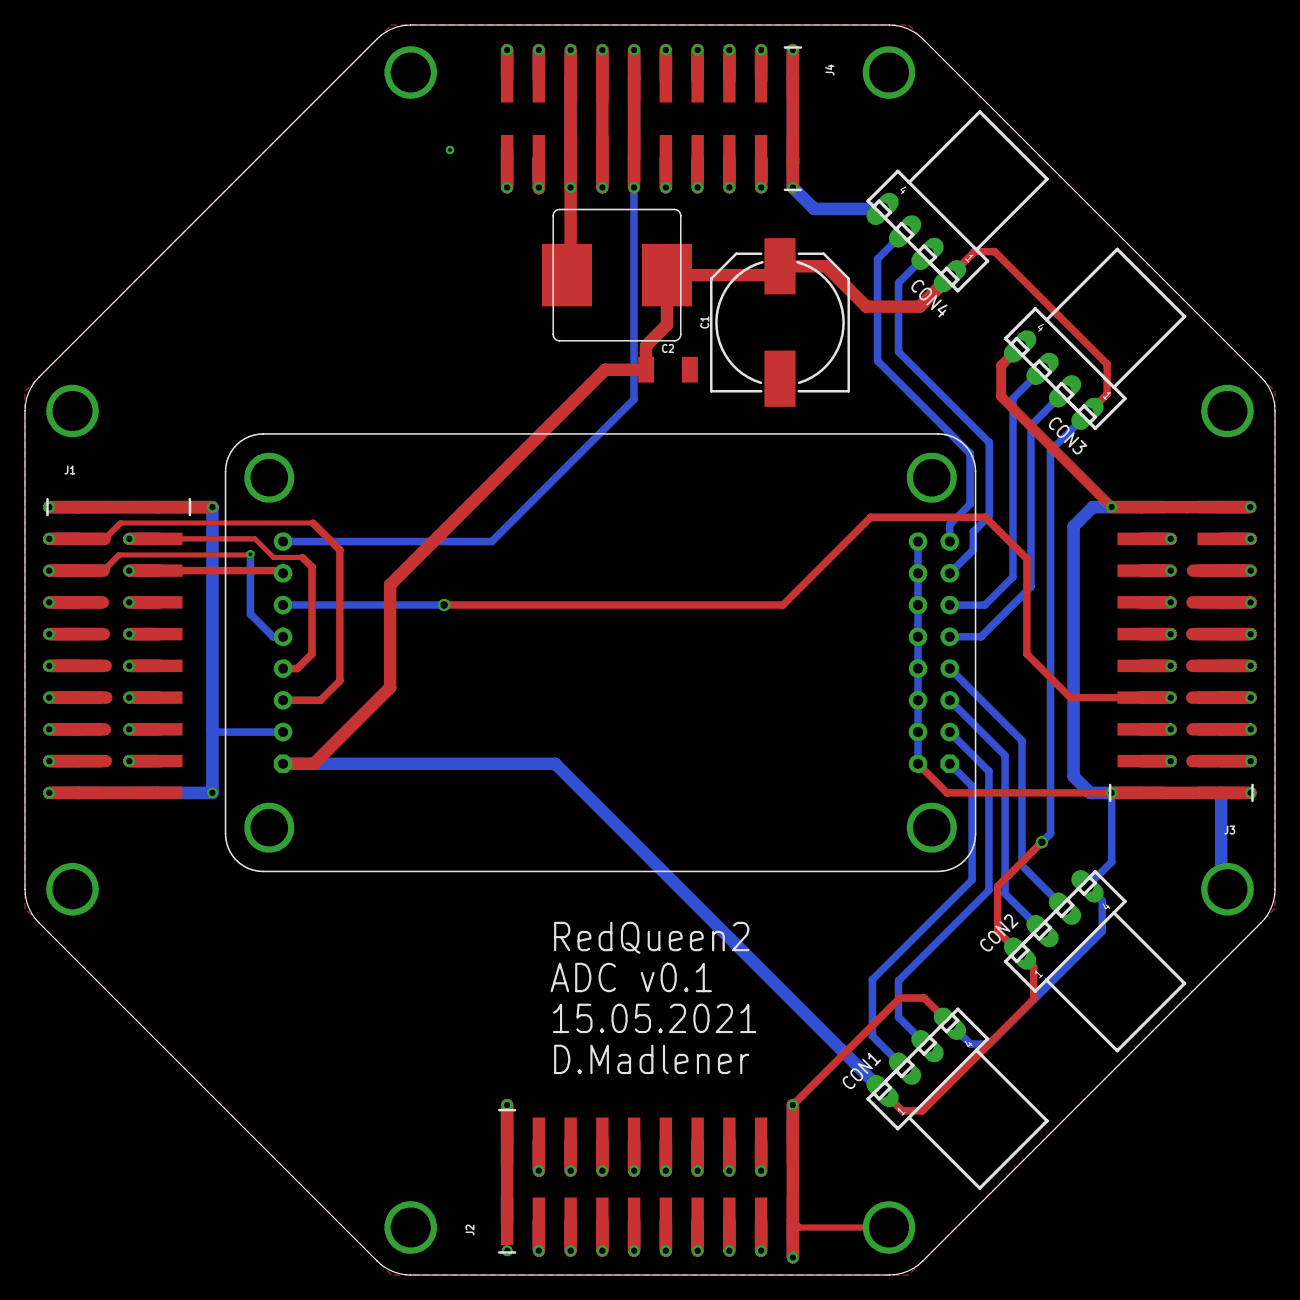
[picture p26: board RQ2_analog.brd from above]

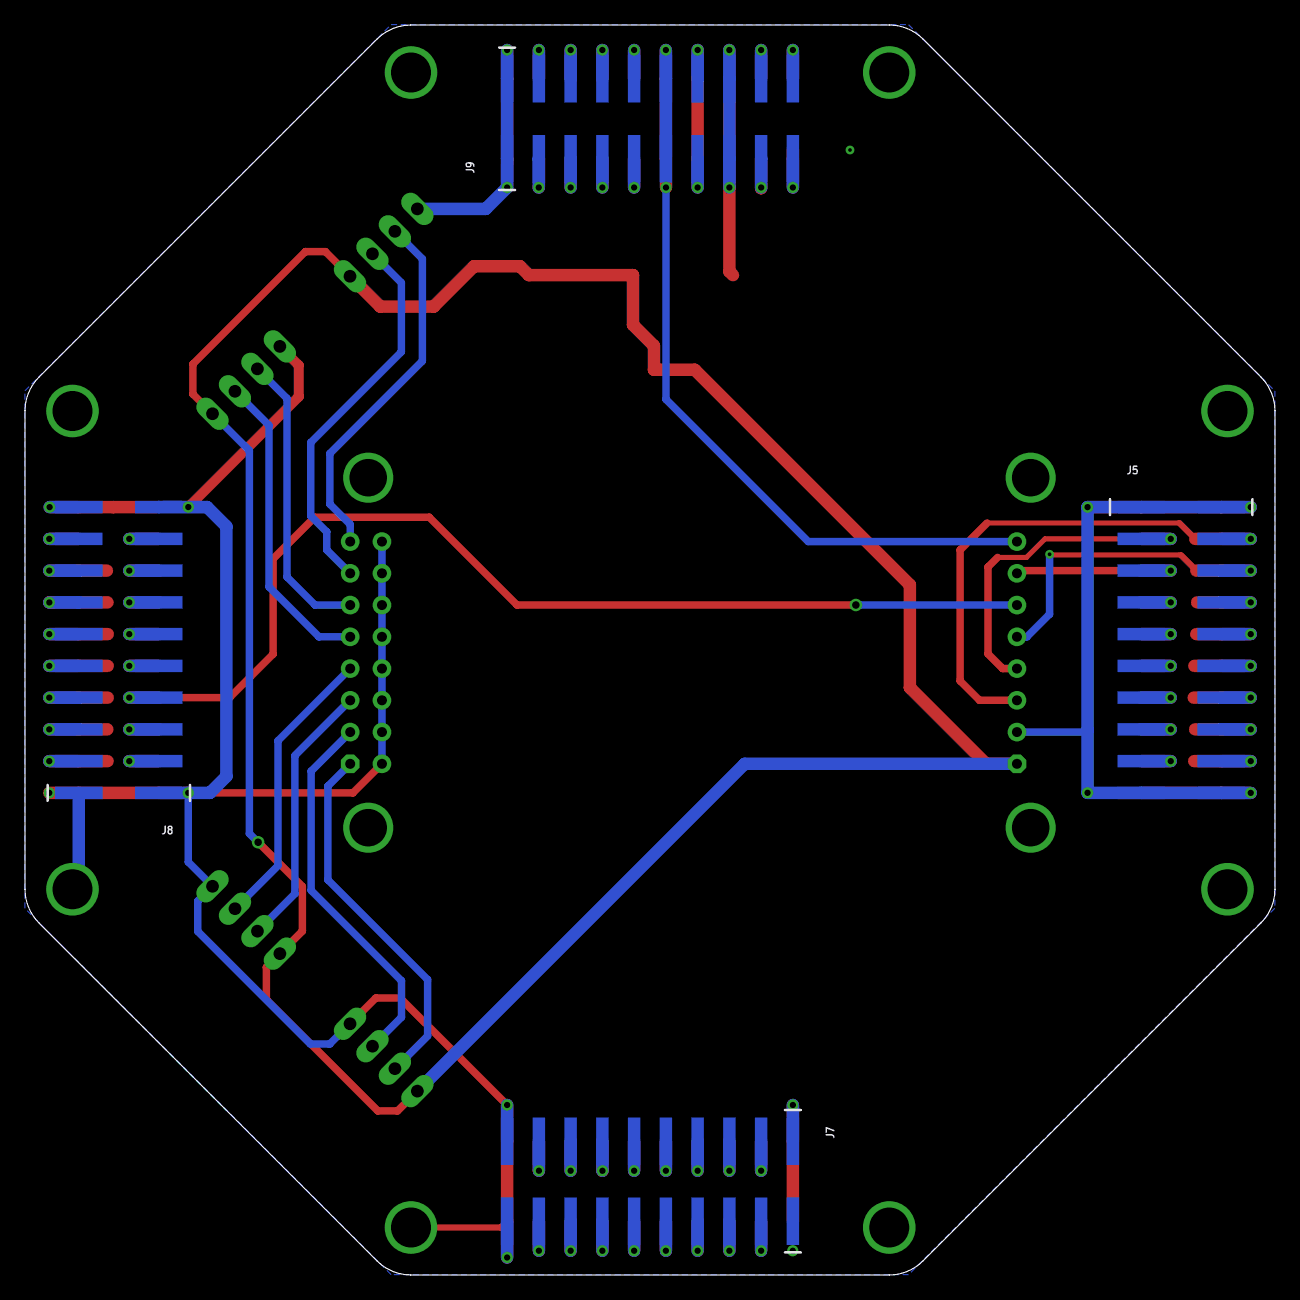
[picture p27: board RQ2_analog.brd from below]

Board: 2 copper layers, 100.0 x 100.0 mm, 16 parts (4 on the bottom side), 72 nets.

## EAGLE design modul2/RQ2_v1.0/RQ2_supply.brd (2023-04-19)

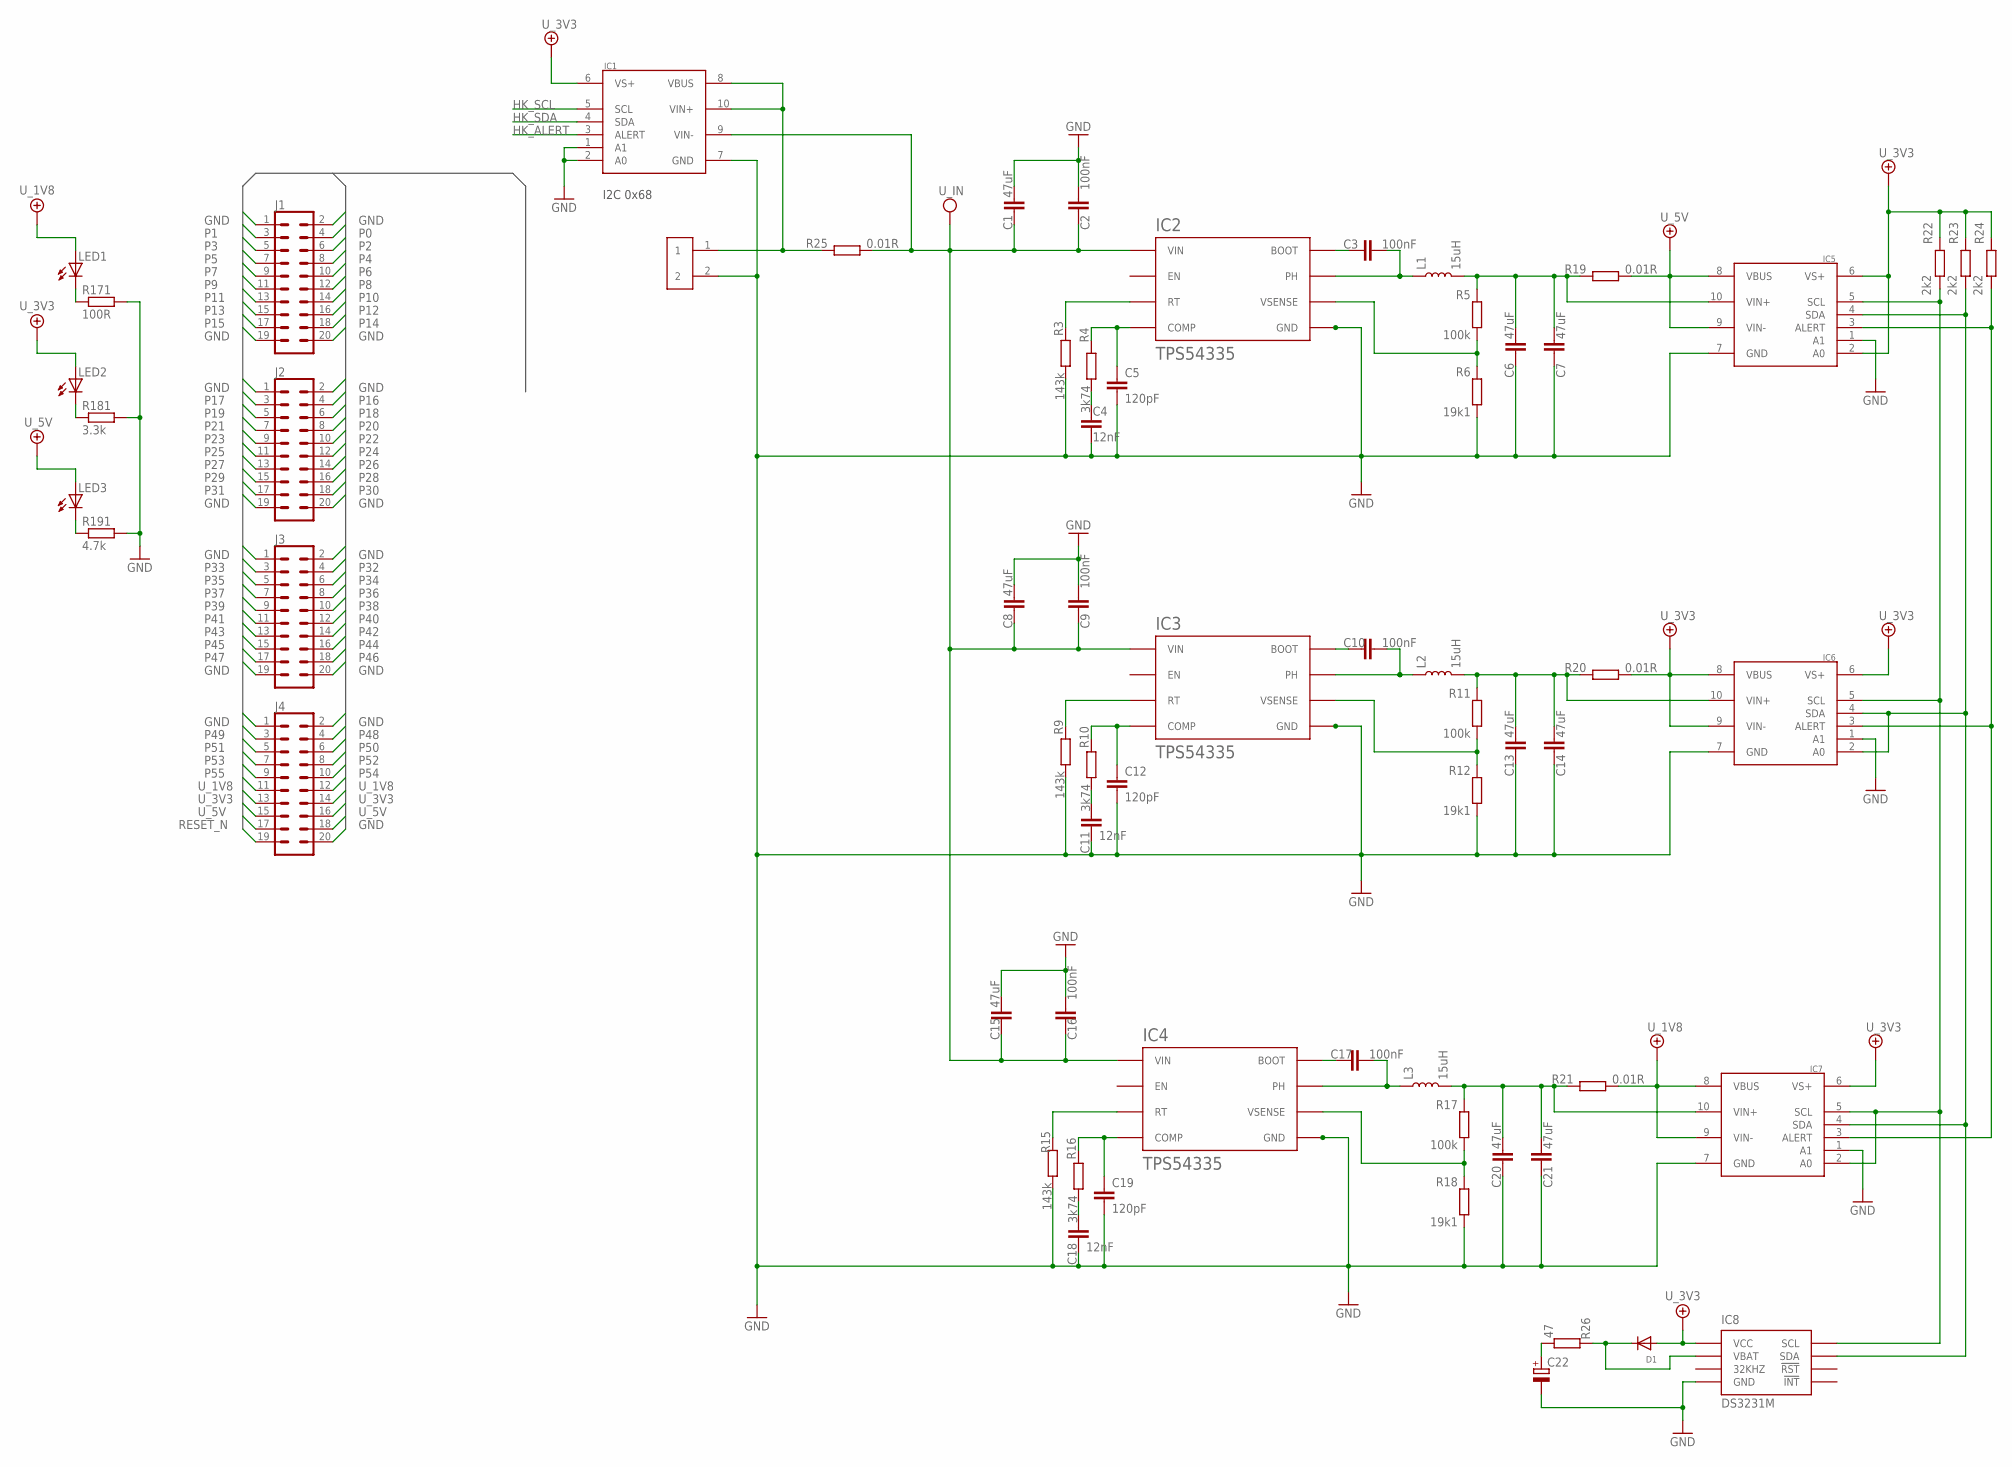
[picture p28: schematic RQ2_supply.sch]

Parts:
C1, C6, C7, C8, C13, C14, C15, C20, C21: 47uF; 1206
C2, C9, C16: 100nF; 0603
C3, C10, C17: 100nF; 0402
C4, C11, C18: 12nF; C0402
C5, C12, C19: 120pF; C0402
C22: CPOL-EUDHL_21.5; DHL_21.5
D1: DIODESOD-123; SOD-123
IC1, IC5, IC6, IC7: INA226; VSSOP-10
IC2, IC3, IC4: TPS54335ADRCR; VSON-10
IC8: DS3231M; SO-8
J1, J2, J3, J4: CONN_10X2; 2X10
L1, L2, L3: 15uH; YSPIA0850
LED1, LED2, LED3: LEDSML0805; SML0805
R3, R9, R15: 143k; R0402
R4, R10, R16: 3k74; R0402
R5, R11, R17: 100k; R0402
R6, R12, R18: 19k1; R0402
R19, R20, R21, R25: 0.01R; R1206
R22, R23, R24: 2k2; R0402
R26: 47; R0603
R171: 100R; R0805
R181: 3.3k; R0805
R191: 4.7k; R0805
U$1: XT_CONN; XT30_PCB

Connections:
DCDC_BOOT: C3.2, IC2.9 (BOOT)
DCDC_BOOT1: C10.2, IC3.9 (BOOT)
DCDC_BOOT2: C17.2, IC4.9 (BOOT)
DCDC_COMP: C5.1, IC2.7 (COMP), R4.1
DCDC_COMP1: C12.1, IC3.7 (COMP), R10.1
DCDC_COMP2: C19.1, IC4.7 (COMP), R16.1
DCDC_PH: C3.1, IC2.2 (PH), L1.1
DCDC_PH1: C10.1, IC3.2 (PH), L2.1
DCDC_PH2: C17.1, IC4.2 (PH), L3.1
DCDC_RT: IC2.10 (RT), R3.1
DCDC_RT1: IC3.10 (RT), R9.1
DCDC_RT2: IC4.10 (RT), R15.1
GND: C1.2, C2.1, C4.2, C5.2, C6.1, C7.1, C8.2, C9.1, C11.2, C12.2, C13.1, C14.1, C15.2, C16.1, C18.2, C19.2, C20.1, C21.1, C22.-, IC1.1 (A1), IC1.2 (A0), IC1.7 (GND), IC2.3 (GND), IC2.4 (GND), IC2.5 (GND), IC2.11 (GND), IC3.3 (GND), IC3.4 (GND), IC3.5 (GND), IC3.11 (GND), IC4.3 (GND), IC4.4 (GND), IC4.5 (GND), IC4.11 (GND), IC5.1 (A1), IC5.7 (GND), IC6.1 (A1), IC6.7 (GND), IC7.1 (A1), IC7.7 (GND), IC8.5 (GND), J1.1, J1.2, J1.19, J1.20, J2.1, J2.2, J2.19, J2.20, J3.1, J3.2, J3.19, J3.20, J4.1, J4.2, J4.18, R3.2, R6.1, R9.2, R12.1, R15.2, R18.1, R171.2, R181.2, R191.2, U$1.2
HK_ALERT: IC1.3 (ALERT), IC5.3 (ALERT), IC6.3 (ALERT), IC7.3 (ALERT), R24.1
HK_SCL: IC1.5 (SCL), IC5.5 (SCL), IC6.5 (SCL), IC7.2 (A0), IC7.5 (SCL), IC8.8 (SCL), R22.1
HK_SDA: IC1.4 (SDA), IC5.4 (SDA), IC6.2 (A0), IC6.4 (SDA), IC7.4 (SDA), IC8.7 (SDA), R23.1
unnamed: C4.1, R4.2
unnamed: LED1.C, R171.1
unnamed: LED2.C, R181.1
unnamed: LED3.C, R191.1
unnamed: C11.1, R10.2
unnamed: C18.1, R16.2
P0: J1.4
P1: J1.3
P2: J1.6
P3: J1.5
P4: J1.8
P5: J1.7
P6: J1.10
P7: J1.9
P8: J1.12
P9: J1.11
P10: J1.14
P11: J1.13
P12: J1.16
P13: J1.15
P14: J1.18
P15: J1.17
P16: J2.4
P17: J2.3
P18: J2.6
P19: J2.5
P20: J2.8
P21: J2.7
P22: J2.10
P23: J2.9
P24: J2.12
P25: J2.11
P26: J2.14
P27: J2.13
P28: J2.16
P29: J2.15
P30: J2.18
P31: J2.17
P32: J3.4
P33: J3.3
P34: J3.6
P35: J3.5
P36: J3.8
P37: J3.7
P38: J3.10
P39: J3.9
P40: J3.12
P41: J3.11
P42: J3.14
P43: J3.13
P44: J3.16
P45: J3.15
P46: J3.18
P47: J3.17
P48: J4.4
P49: J4.3
P50: J4.6
P51: J4.5
P52: J4.8
P53: J4.7
P54: J4.10
P55: J4.9
RESET_N: J4.17
RXD: J4.20
TXD: J4.19
U0_1V8: C20.2, C21.2, IC7.10 (VIN+), L3.2, R17.2, R21.2
U0_3V3: C13.2, C14.2, IC6.10 (VIN+), L2.2, R11.2, R20.2
U0_5V: C6.2, C7.2, IC5.10 (VIN+), L1.2, R5.2, R19.2
U0_IN: IC1.8 (VBUS), IC1.10 (VIN+), R25.2, U$1.1
U_1V8: IC7.8 (VBUS), IC7.9 (VIN-), J4.11, J4.12, LED1.A, R21.1
U_3V3: D1.A, IC5.2 (A0), IC6.6 (VS+), IC6.8 (VBUS), IC6.9 (VIN-), IC7.6 (VS+), IC8.2 (VCC), J4.13, J4.14, LED2.A, R20.1, R22.2, R23.2, R24.2
U_5V: IC5.8 (VBUS), IC5.9 (VIN-), J4.15, J4.16, LED3.A, R19.1
U_IN: C1.1, C2.2, C8.1, C9.2, C15.1, C16.2, IC1.9 (VIN-), IC2.1 (VIN), IC3.1 (VIN), IC4.1 (VIN), R25.1
VBAT1: D1.C, IC8.6 (VBAT), R26.1
VCAP: C22.+, R26.2
VSENSE_1V8: IC4.6 (VSENSE), R17.1, R18.2
VSENSE_3V3: IC3.6 (VSENSE), R11.1, R12.2
VSENSE_5V: IC2.6 (VSENSE), R5.1, R6.2

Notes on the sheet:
I2C 0x68

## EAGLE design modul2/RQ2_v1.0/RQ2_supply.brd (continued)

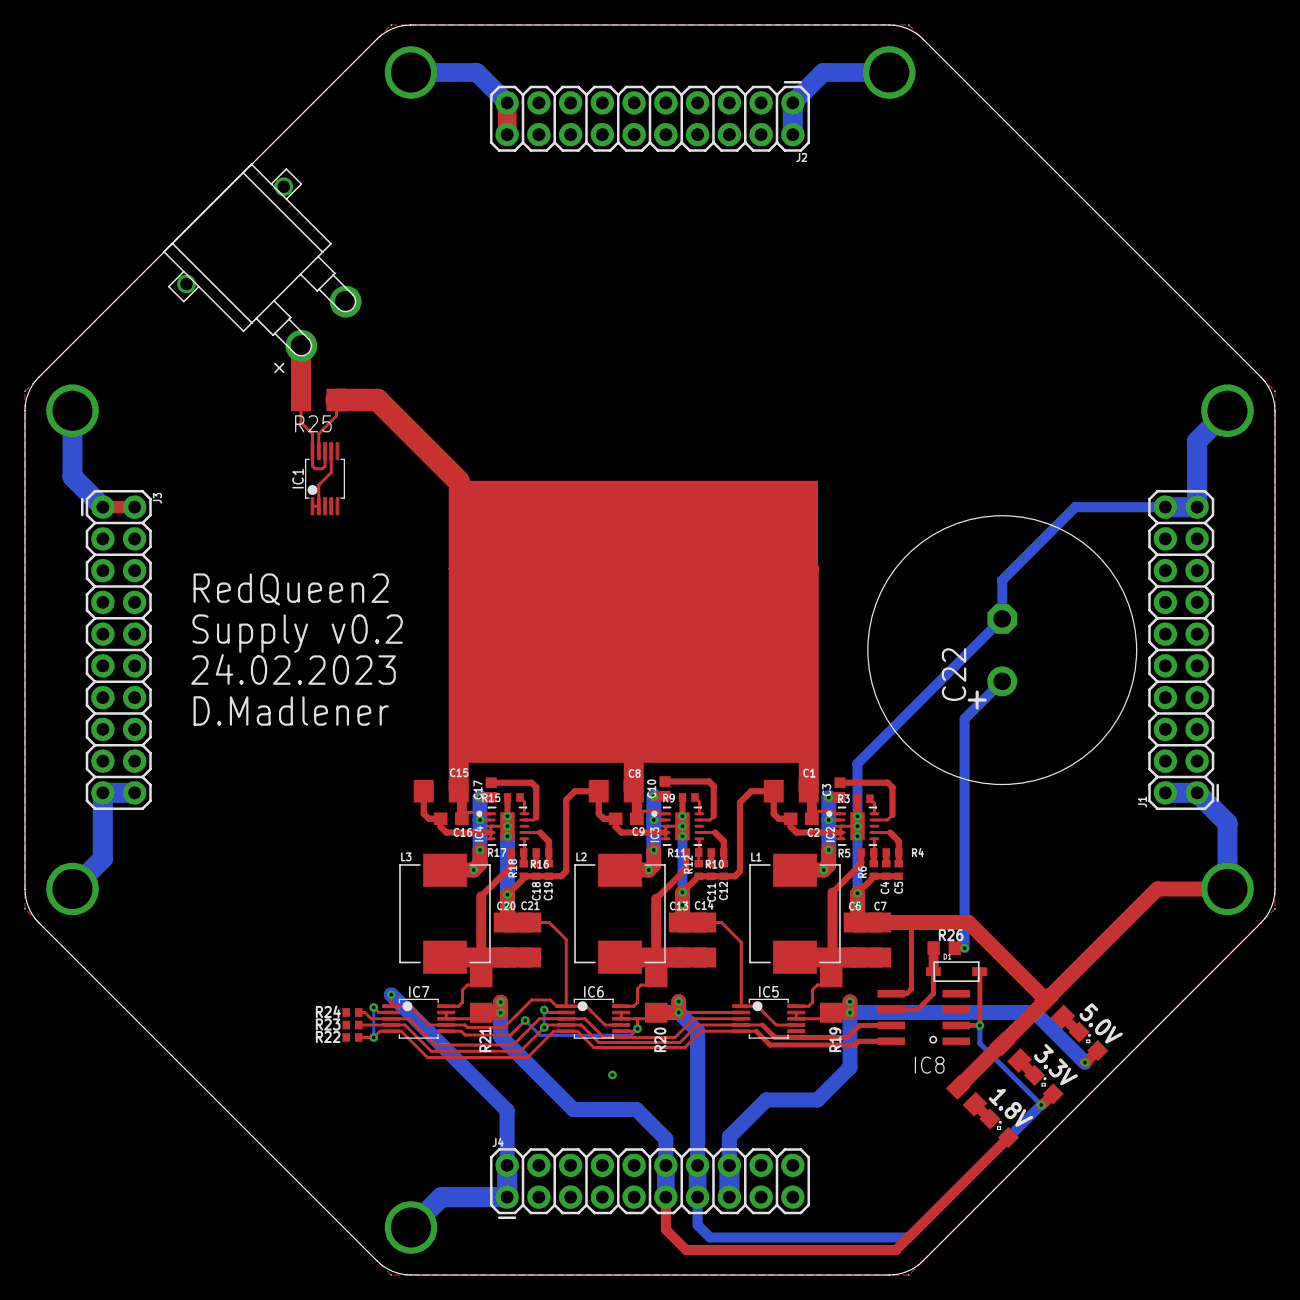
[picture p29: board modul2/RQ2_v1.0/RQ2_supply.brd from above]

Board: 2 copper layers, 100.0 x 100.0 mm, 65 parts (0 on the bottom side), 35 nets.

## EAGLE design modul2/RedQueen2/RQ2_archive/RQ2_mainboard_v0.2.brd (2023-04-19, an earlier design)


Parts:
C1, C2, C3, C4, C5, C6, C7, C8, C9, C10, C11, C12, C13, C14, C16, C17, C18, C19: C-EUC0805; C0805
C15: CPOL-EUDHL_21.5; DHL_21.5
D1: SS14; SMA_403D
IC1: P2X8C4M64P; TQFP100
IC2: 25F32006WSOI; SO08-EIAJ
IC3, IC4: IS66WVH16M8BLL-100B1LI; BGA-24
IC5: PCF8574T; SO16W
J1, J2, J3, J4, J5, J7, J8, J9: CONN_10X2SMT; 2X10_SMT
J6: CONN_04; 1X04
J11: CONN_04X2; 2X4
J12: CONN_05X2SHD; 2X5-SHROUDED
J13: CONN_24SERVO_8; 3X8
R1, R2, R3, R16: 10k; R0603
R4: 240; R0603
R5, R6, R7, R8, R9, R10, R11, R12, R13, R14: 4k7; R0603
R15: 47; R0603
R17, R18, R19, R20, R21, R22: 12; R0402
RN1, RN2, RN3, RN4, RN5, RN6, RN7, RN8, RN9, RN10, RN15, RN16: 4R-N0603-ARV; 0603-ARV
U1: PCA9685; TSSOP28
U$2: MICRO_SD_CONNECTORMOLEX_HINGE; MICRO_SD
U$3: DS3231M; SO-8
Y1: CRYSTALSMD-5X3.2-2PAD; CRYSTAL-SMD-5X3.2-2PAD

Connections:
BOOT_MISO: IC2.2 (MISO), R4.1, RN16.3 (1)
BOOT_MOSI: IC2.5 (MOSI), J11.6, J11.8, RN16.4 (1), U$2.3 (DIN)
BOOT_SCLK: IC2.6 (SCK), RN15.1, U$2.2 (CS)
FLASH_A_CS: IC3.C2 (RFU_CS#), R17.2
FLASH_A_INT: IC3.A5 (RFU_INT#), R21.2
FLASH_B_CS: IC4.C2 (RFU_CS#), R19.2
FLASH_B_INT: IC4.A5 (RFU_INT#), R22.2
FLASH_CS: IC2.1 (CS), J11.4, R1.1
GND: C1.2, C2.2, C3.2, C4.2, C5.2, C6.2, C7.2, C8.2, C9.2, C10.2, C11.2, C12.2, C13.2, C14.2, C15.-, C16.2, C17.2, C18.2, C19.2, IC1.1 (TEST), IC1.EPAD (GND), IC2.4 (GND), IC3.B3 (VSS), IC3.C1 (VSSQ), IC3.E5 (VSSQ), IC4.B3 (VSS), IC4.C1 (VSSQ), IC4.E5 (VSSQ), IC5.1 (A0), IC5.2 (A1), IC5.3 (A2), IC5.8 (VSS), J1.1, J1.2, J1.19, J1.20, J2.1, J2.2, J2.19, J2.20, J3.1, J3.2, J3.19, J3.20, J4.1, J4.2, J4.3, J4.4, J5.1, J5.2, J5.19, J5.20, J6.4, J7.1, J7.2, J7.19, J7.20, J8.1, J8.2, J8.19, J8.20, J9.1, J9.2, J9.3, J9.4, J12.9, J13.1, J13.4, J13.7, J13.10, J13.13, J13.16, J13.19, J13.22, R2.2, U1.1 (A0), U1.2 (A1), U1.3 (A2), U1.4 (A3), U1.5 (A4), U1.14 (GND), U1.23 (#OE), U1.24 (A5), U1.25 (EXTCLK), U$2.6 (GND), U$3.5 (GND)
GPIO0: J3.3, J8.4, RN9.1
GPIO1: J3.4, J8.3, RN9.2 (1)
GPIO2: J3.5, J8.6, RN9.3 (1)
GPIO3: J3.6, J8.5, RN9.4 (1)
GPIO4: J3.7, J8.8, RN10.1
GPIO5: J3.8, J8.7, RN10.2 (1)
GPIO6: J3.9, J8.10, RN10.3 (1)
GPIO7: J3.10, J8.9, RN10.4 (1)
I2C0_PORT0: IC5.4 (P0), J12.1
I2C0_PORT1: IC5.5 (P1), J12.2
I2C0_PORT2: IC5.6 (P2), J12.3
I2C0_PORT3: IC5.7 (P3), J12.4
I2C0_PORT4: IC5.9 (P4), J12.5
I2C0_PORT5: IC5.10 (P5), J12.6
I2C0_PORT6: IC5.11 (P6), J12.7
I2C0_PORT7: IC5.12 (P7), J12.8
I2C_SCL0: IC5.14 (SCL), J2.3, J7.4, R5.1, RN3.1
I2C_SCL1: J2.5, J7.6, R7.1, RN3.3 (1), U1.26 (SCL)
I2C_SCL2: J2.7, J7.8, R9.1, RN4.1
I2C_SCL3: J2.9, J7.10, R11.1, RN4.3 (1)
I2C_SDA0: IC5.15 (SDA), J2.4, J7.3, R6.1, RN3.2 (1)
I2C_SDA1: J2.6, J7.5, R8.1, RN3.4 (1), U1.27 (SDA)
I2C_SDA2: J2.8, J7.7, R10.1, RN4.2 (1)
I2C_SDA3: J2.10, J7.9, R12.1, RN4.4 (1)
unnamed: J11.7, R2.1
unnamed: J11.5, R3.1
unnamed: R4.2, U$2.7 (DOUT)
P0: IC1.3 (P0), RN1.8 (2)
P1: IC1.4 (P1), RN1.7 (2)
P2: IC1.6 (P2), RN1.6 (2)
P3: IC1.7 (P3), RN1.5 (2)
P4: IC1.9 (P4), RN2.8 (2)
P5: IC1.10 (P5), RN2.7 (2)
P6: IC1.12 (P6), RN2.6 (2)
P7: IC1.13 (P7), RN2.5 (2)
P8: IC1.15 (P8), RN7.8 (2)
P9: IC1.16 (P9), RN7.7 (2)
P10: IC1.18 (P10), RN7.6 (2)
P11: IC1.19 (P11), RN7.5 (2)
P12: IC1.21 (P12), RN8.8 (2)
P13: IC1.22 (P13), RN8.7 (2)
P14: IC1.24 (P14), RN8.6 (2)
P15: IC1.25 (P15), RN8.5 (2)
P16: IC1.27 (P16), RN3.8 (2)
P17: IC1.28 (P17), RN3.7 (2)
P18: IC1.30 (P18), RN3.6 (2)
P19: IC1.31 (P19), RN3.5 (2)
P20: IC1.33 (P20), RN4.8 (2)
P21: IC1.34 (P21), RN4.7 (2)
P22: IC1.36 (P22), RN4.6 (2)
P23: IC1.37 (P23), RN4.5 (2)
P24: IC1.39 (P24), RN5.8 (2)
P25: IC1.40 (P25), RN5.7 (2)
P26: IC1.42 (P26), RN5.6 (2)
P27: IC1.43 (P27), RN5.5 (2)
P28: IC1.45 (P28), RN6.8 (2)
P29: IC1.46 (P29), RN6.7 (2)
P30: IC1.48 (P30), RN6.6 (2)
P31: IC1.49 (P31), RN6.5 (2)
P32: IC1.53 (P32), RN9.8 (2)
P33: IC1.54 (P33), RN9.7 (2)
P34: IC1.56 (P34), RN9.6 (2)
P35: IC1.57 (P35), RN9.5 (2)
P36: IC1.59 (P36), RN10.8 (2)
P37: IC1.60 (P37), RN10.7 (2)
P38: IC1.62 (P38), RN10.6 (2)
P39: IC1.63 (P39), RN10.5 (2)
P40: IC1.65 (P40), IC3.D3 (DQ0), IC4.D3 (DQ0)
P41: IC1.66 (P41), IC3.D2 (DQ1), IC4.D2 (DQ1)
P42: IC1.68 (P42), IC3.C4 (DQ2), IC4.C4 (DQ2)
P43: IC1.69 (P43), IC3.D4 (DQ3), IC4.D4 (DQ3)
P44: IC1.71 (P44), IC3.D5 (DQ4), IC4.D5 (DQ4)
P45: IC1.72 (P45), IC3.E3 (DQ5), IC4.E3 (DQ5)
P46: IC1.74 (P46), IC3.E2 (DQ6), IC4.E2 (DQ6)
P47: IC1.75 (P47), IC3.E1 (DQ7), IC4.E1 (DQ7)
P48: IC1.77 (P48), IC3.B2 (CK)
P49: IC1.78 (P49), IC4.B2 (CK)
P50: IC1.80 (P50), IC3.C3 (RWDS)
P51: IC1.81 (P51), IC4.C3 (RWDS)
P52: IC1.83 (P52), R17.1, R18.1
P53: IC1.84 (P53), R19.1, R20.1
P54: IC1.86 (P54), R21.1, R22.1
P55: IC1.87 (P55), IC3.A4 (RESET#), IC4.A4 (RESET#)
P56: IC1.89 (P56), RN16.8 (2)
P57: IC1.90 (P57), RN16.7 (2)
P58: IC1.92 (P58), RN16.6 (2)
P59: IC1.93 (P59), RN16.5 (2)
P60: IC1.95 (P60), RN15.8 (2)
P61: IC1.96 (P61), RN15.7 (2)
P62: IC1.98 (P62), RN15.6 (2)
P63: IC1.99 (P63), RN15.5 (2)
PWM0: J3.11, J8.12, U1.6 (PWM0)
PWM1: J3.12, J8.11, U1.7 (PWM1)
PWM2: J3.13, J8.14, U1.8 (PWM2)
PWM3: J3.14, J8.13, U1.9 (PWM3)
PWM4: J3.15, J8.16, U1.10 (PWM4)
PWM5: J3.16, J8.15, U1.11 (PWM5)
PWM6: J3.17, J8.18, U1.12 (PWM6)
PWM7: J3.18, J8.17, U1.13 (PWM7)
PWM8: J13.3, U1.15 (PWM8)
PWM9: J13.6, U1.16 (PWM9)
PWM10: J13.9, U1.17 (PWM10)
PWM11: J13.12, U1.18 (PWM11)
PWM12: J13.15, U1.19 (PWM12)
PWM13: J13.18, U1.20 (PWM13)
PWM14: J13.21, U1.21 (PWM14)
PWM15: J13.24, U1.22 (PWM15)
RAM_A_CS: IC3.A3 (CS#_DNU), R18.2
RAM_B_CS: IC4.A3 (CS#_DNU), R20.2
RESET_N: IC1.100 (RESN), J4.18, J6.3, J9.17, J11.2, R16.1
RTC_SCL: R13.1, RN16.1, U$3.8 (SCL)
RTC_SDA: R14.1, RN16.2 (1), U$3.7 (SDA)
RXD: J4.19, J6.2, J9.20, RN15.4 (1)
SD_CLK: J11.3, RN15.2 (1), U$2.5 (SCLK)
SPI_MISO0: J1.5, J5.6, RN1.3 (1)
SPI_MISO1: J1.9, J5.10, RN2.3 (1)
SPI_MISO2: J1.13, J5.14, RN7.3 (1)
SPI_MISO3: J1.17, J5.18, RN8.3 (1)
SPI_MOSI0: J1.4, J5.3, RN1.2 (1)
SPI_MOSI1: J1.8, J5.7, RN2.2 (1)
SPI_MOSI2: J1.12, J5.11, RN7.2 (1)
SPI_MOSI3: J1.16, J5.15, RN8.2 (1)
SPI_SCLK0: J1.3, J5.4, RN1.1
SPI_SCLK1: J1.7, J5.8, RN2.1
SPI_SCLK2: J1.11, J5.12, RN7.1
SPI_SCLK3: J1.15, J5.16, RN8.1
SPI_SS0: J1.6, J5.5, RN1.4 (1)
SPI_SS1: J1.10, J5.9, RN2.4 (1)
SPI_SS2: J1.14, J5.13, RN7.4 (1)
SPI_SS3: J1.18, J5.17, RN8.4 (1)
TXD: J4.20, J6.1, J9.19, RN15.3 (1)
UART_RX0: J2.11, J7.12, RN5.1
UART_RX1: J2.13, J7.14, RN5.3 (1)
UART_RX2: J2.15, J7.16, RN6.1
UART_RX3: J2.17, J7.18, RN6.3 (1)
UART_TX0: J2.12, J7.11, RN5.2 (1)
UART_TX1: J2.14, J7.13, RN5.4 (1)
UART_TX2: J2.16, J7.15, RN6.2 (1)
UART_TX3: J2.18, J7.17, RN6.4 (1)
U_1V8: C1.1, C2.1, C3.1, C4.1, C5.1, C6.1, C7.1, C8.1, IC1.2 (VDD), IC1.8 (VDD), IC1.14 (VDD), IC1.20 (VDD), IC1.26 (VDD), IC1.32 (VDD), IC1.38 (VDD), IC1.44 (VDD), IC1.52 (VDD), IC1.58 (VDD), IC1.64 (VDD), IC1.70 (VDD), IC1.76 (VDD), IC1.82 (VDD), IC1.88 (VDD), IC1.94 (VDD), J4.5, J4.6, J4.7, J4.8, J9.5, J9.6, J9.7, J9.8
U_3V3: C9.1, C10.1, C11.1, C12.1, C13.1, C14.1, C16.1, C18.1, C19.1, D1.A, IC1.5 (V0003), IC1.11 (V0407), IC1.17 (V0811), IC1.23 (V1215), IC1.29 (V1619), IC1.35 (V2023), IC1.41 (V2427), IC1.47 (V2831), IC1.55 (V3235), IC1.61 (V3639), IC1.67 (V4043), IC1.73 (V4447), IC1.79 (V4851), IC1.85 (V5255), IC1.91 (V5659), IC1.97 (V6063), IC2.3 (WP), IC2.7 (HOLD), IC2.8 (VCC), IC3.B4 (VCC), IC3.D1 (VCCQ), IC3.E4 (VCCQ), IC4.B4 (VCC), IC4.D1 (VCCQ), IC4.E4 (VCCQ), IC5.16 (VDD), J4.9, J4.10, J4.11, J4.12, J9.9, J9.10, J9.11, J9.12, J12.10, R1.2, R3.2, R5.2, R6.2, R7.2, R8.2, R9.2, R10.2, R11.2, R12.2, R13.2, R14.2, R16.2, U$2.4 (VDD), U$3.2 (VCC)
U_5V: C17.1, J4.13, J4.14, J4.15, J4.16, J9.13, J9.14, J9.15, J9.16, J13.2, J13.5, J13.8, J13.11, J13.14, J13.17, J13.20, J13.23, U1.28 (VDD)
VBAT: D1.C, R15.1, U$3.6 (VBAT)
VCAP: C15.+, R15.2
XIN: IC1.51 (XI), Y1.P$2 (2)
XOUT: IC1.50 (XO), Y1.P$1 (1)



Board: 2 copper layers, 100.0 x 100.0 mm, 75 parts (29 on the bottom side), 155 nets.

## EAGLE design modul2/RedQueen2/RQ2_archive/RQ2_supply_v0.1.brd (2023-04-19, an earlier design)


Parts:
C1, C2, C3: CPOL-EUSANYO_E9; SANYO-OSCON_E9
C4: C-EUC0805; C0805
IC1: PCF8574T; SO16W
IC2: LM339D; SO14
J1, J2, J3, J4: CONN_10X2; 2X10
LED1, LED2, LED3, LED4, LED5, LED6, LED7, LED8, LED9, LED10, LED11: LEDSML0805; SML0805
P0, P1, P2, P3: 2PIN; B2B-PH-K-S
R1, R2: 18k; R0805
R3, R4, R5, R6: 12k; R0805
R7, R8, R9, R10: 22k; R0805
R11, R12, R13, R14: 10k; R0805
R15, R16: R-EU_R0805; R0805
R17: 100R; R0805
R18, R20, R21, R22, R23: 3.3k; R0805
R19: 4.7k; R0805
R24, R25, R26, R27: 1k; R0805
U1, U2, U3: DCDC_CONVERTER
U$1: XT_CONN; XT30_PCB
U$3: ADC-4CH-ADS1115
ULN1: ULN2803SOICW; SO18L

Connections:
COMPARE: C4.1, IC2.4 (-IN), IC2.6 (-IN), IC2.8 (-IN), IC2.10 (-IN), R1.1, R2.2
GND: C1.-, C2.-, C3.-, C4.2, IC1.1 (A0), IC1.3 (A2), IC1.8 (VSS), IC2.12 (GND), J1.1, J1.2, J1.19, J1.20, J2.1, J2.2, J2.19, J2.20, J3.1, J3.2, J3.19, J3.20, J4.1, J4.2, J4.3, J4.4, R2.1, R7.1, R8.1, R9.1, R10.1, R16.2, R17.2, R18.2, R19.2, R20.1, R21.1, R22.1, R23.1, U1.GND, U2.GND, U3.GND, U$1.2, U$3.2 (GND), U$3.5 (ADDR), ULN1.9
GPIO0: J3.3, ULN1.1, ULN1.2
GPIO1: J3.4, ULN1.3, ULN1.4
GPIO2: J3.5, ULN1.5, ULN1.6
GPIO3: J3.6, ULN1.7, ULN1.8
GPIO4: IC1.13 (!INT), J3.7
GPIO5: J3.8
GPIO6: J3.9
GPIO7: J3.10
I2C_SCL0: IC1.14 (SCL), J2.3, U$3.3 (SCL)
I2C_SCL1: J2.5
I2C_SCL2: J2.7
I2C_SCL3: J2.9
I2C_SDA0: IC1.15 (SDA), J2.4, U$3.4 (SDA)
I2C_SDA1: J2.6
I2C_SDA2: J2.8
I2C_SDA3: J2.10
LED4: LED4.C, R20.2
LED5: LED5.C, R21.2
LED6: LED6.C, R22.2
LED7: LED7.C, R23.2
unnamed: R15.2, R16.1, U$3.10 (A3)
unnamed: LED1.C, R17.1
unnamed: LED2.C, R18.1
unnamed: LED3.C, R19.1
unnamed: LED8.C, R24.2
unnamed: LED9.C, R25.2
unnamed: LED10.C, R26.2
unnamed: LED11.C, R27.2
NOT_BLOWN0: IC1.4 (P0), IC2.2 (OUT), R14.1
NOT_BLOWN1: IC1.5 (P1), IC2.1 (OUT), R13.1
NOT_BLOWN2: IC1.6 (P2), IC2.14 (OUT), R12.1
NOT_BLOWN3: IC1.7 (P3), IC2.13 (OUT), R11.1
P4: IC1.9 (P4), LED4.A
P5: IC1.10 (P5), LED5.A
P6: IC1.11 (P6), LED6.A
P7: IC1.12 (P7), LED7.A
PWM0: J3.11
PWM1: J3.12
PWM2: J3.13
PWM3: J3.14
PWM4: J3.15
PWM5: J3.16
PWM6: J3.17
PWM7: J3.18
PYRO0: P0.2, R3.2, R24.1, ULN1.17, ULN1.18
PYRO1: P1.2, R4.2, R25.1, ULN1.15, ULN1.16
PYRO2: P2.2, R5.2, R26.1, ULN1.13, ULN1.14
PYRO3: P3.2, R6.2, R27.1, ULN1.11, ULN1.12
PYRO_PROBE0: IC2.5 (+IN), R3.1, R7.2
PYRO_PROBE1: IC2.7 (+IN), R4.1, R8.2
PYRO_PROBE2: IC2.9 (+IN), R5.1, R9.2
PYRO_PROBE3: IC2.11 (+IN), R6.1, R10.2
SPI_MISO0: J1.5
SPI_MISO1: J1.9
SPI_MISO2: J1.13
SPI_MISO3: J1.17
SPI_MOSI0: J1.4
SPI_MOSI1: J1.8
SPI_MOSI2: J1.12
SPI_MOSI3: J1.16
SPI_SCLK0: J1.3
SPI_SCLK1: J1.7
SPI_SCLK2: J1.11
SPI_SCLK3: J1.15
SPI_SS0: J1.6
SPI_SS1: J1.10
SPI_SS2: J1.14
SPI_SS3: J1.18
UART_RX0: J2.11
UART_RX1: J2.13
UART_RX2: J2.15
UART_RX3: J2.17
UART_TX0: J2.12
UART_TX1: J2.14
UART_TX2: J2.16
UART_TX3: J2.18
U_1V8: C1.+, J4.5, J4.6, J4.7, J4.8, LED1.A, U1.VOUT (OUT), U$3.7 (A0)
U_3V3: C2.+, IC1.2 (A1), IC1.16 (VDD), J4.9, J4.10, J4.11, J4.12, LED2.A, LED8.A, LED9.A, LED10.A, LED11.A, R11.2, R12.2, R13.2, R14.2, U2.VOUT (OUT), U$3.1 (VDD), U$3.8 (A1)
U_5V: C3.+, J4.13, J4.14, J4.15, J4.16, LED3.A, U3.VOUT (OUT), U$3.9 (A2)
U_IN: P0.1, P1.1, P2.1, P3.1, R1.2, R15.1, U1.EN, U1.VIN (IN), U2.EN, U2.VIN (IN), U3.EN, U3.VIN (IN), U$1.1, ULN1.10
V+: IC2.3 (V+)



Board: 2 copper layers, 100.0 x 100.0 mm, 58 parts (8 on the bottom side), 41 nets.

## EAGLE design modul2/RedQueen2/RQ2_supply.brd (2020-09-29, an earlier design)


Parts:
C1, C2, C3: CPOL-EUC; PANASONIC_C
C4: C-EUC0805; C0805
IC1: PCF8574T; SO16W
IC2: LM339D; SO14
J1, J2, J3, J4: CONN_10X2; 2X10
P0, P1, P2, P3: 2PIN; B2B-PH-K-S
R1, R2: R-EU_R0805; R0805
RN1: 4k7; 0603-ARV
RN2, RN3: 47k; 0603-ARV
U1, U2, U3: DCDC_CONVERTER
U$1: XT_CONN; XT30_PCB
ULN1: ULN2803SOICW; SO18L

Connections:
GND: C1.-, C2.-, C3.-, C4.2, IC1.1 (A0), IC1.2 (A1), IC1.3 (A2), IC1.8 (VSS), IC2.12 (GND), J1.1, J1.2, J1.19, J1.20, J2.1, J2.2, J2.19, J2.20, J3.1, J3.2, J3.19, J3.20, J4.1, J4.2, J4.3, J4.4, R2.1, RN3.1, RN3.2 (1), RN3.3 (1), RN3.4 (1), U1.GND, U2.GND, U3.GND, U$1.2, ULN1.9
GPIO0: J3.3, ULN1.1, ULN1.2
GPIO1: J3.4, ULN1.3, ULN1.4
GPIO2: J3.5, ULN1.5, ULN1.6
GPIO3: J3.6, ULN1.7, ULN1.8
GPIO4: J3.7
GPIO5: J3.8
GPIO6: J3.9
GPIO7: J3.10
I2C_SCL0: J2.3
I2C_SCL1: J2.5
I2C_SCL2: J2.7
I2C_SCL3: J2.9
I2C_SDA0: J2.4
I2C_SDA1: J2.6
I2C_SDA2: J2.8
I2C_SDA3: J2.10
unnamed: IC1.4 (P0), IC2.2 (OUT), RN1.1
unnamed: IC1.5 (P1), IC2.1 (OUT), RN1.2 (1)
unnamed: IC1.6 (P2), IC2.14 (OUT), RN1.3 (1)
unnamed: IC1.7 (P3), IC2.13 (OUT), RN1.4 (1)
unnamed: IC2.5 (+IN), RN2.1, RN3.8 (2)
unnamed: IC2.7 (+IN), RN2.2 (1), RN3.7 (2)
unnamed: IC2.9 (+IN), RN2.3 (1), RN3.6 (2)
unnamed: IC2.11 (+IN), RN2.4 (1), RN3.5 (2)
unnamed: C4.1, IC2.4 (-IN), IC2.6 (-IN), IC2.8 (-IN), IC2.10 (-IN), R1.1, R2.2
PWM0: J3.11
PWM1: J3.12
PWM2: J3.13
PWM3: J3.14
PWM4: J3.15
PWM5: J3.16
PWM6: J3.17
PWM7: J3.18
PYRO0: P0.2, RN2.8 (2), ULN1.17, ULN1.18
PYRO1: P1.2, RN2.7 (2), ULN1.15, ULN1.16
PYRO2: P2.2, RN2.6 (2), ULN1.13, ULN1.14
PYRO3: P3.2, RN2.5 (2), ULN1.11, ULN1.12
SPI_MISO0: J1.5
SPI_MISO1: J1.9
SPI_MISO2: J1.13
SPI_MISO3: J1.17
SPI_MOSI0: J1.4
SPI_MOSI1: J1.8
SPI_MOSI2: J1.12
SPI_MOSI3: J1.16
SPI_SCLK0: J1.3
SPI_SCLK1: J1.7
SPI_SCLK2: J1.11
SPI_SCLK3: J1.15
SPI_SS0: J1.6
SPI_SS1: J1.10
SPI_SS2: J1.14
SPI_SS3: J1.18
UART_RX0: J2.11
UART_RX1: J2.13
UART_RX2: J2.15
UART_RX3: J2.17
UART_TX0: J2.12
UART_TX1: J2.14
UART_TX2: J2.16
UART_TX3: J2.18
U_1V8: C1.+, J4.5, J4.6, J4.7, J4.8, U1.VOUT (OUT)
U_3V3: C2.+, IC1.16 (VDD), J4.9, J4.10, J4.11, J4.12, RN1.5 (2), RN1.6 (2), RN1.7 (2), RN1.8 (2), U2.VOUT (OUT)
U_5V: C3.+, J4.13, J4.14, J4.15, J4.16, U3.VOUT (OUT)
U_IN: J4.17, J4.18, J4.19, J4.20, P0.1, P1.1, P2.1, P3.1, R1.2, U1.EN, U1.VIN (IN), U2.EN, U2.VIN (IN), U3.EN, U3.VIN (IN), U$1.1, ULN1.10
V+: IC2.3 (V+)


Board: 2 copper layers, 100.0 x 100.0 mm, 24 parts (0 on the bottom side), 22 nets.

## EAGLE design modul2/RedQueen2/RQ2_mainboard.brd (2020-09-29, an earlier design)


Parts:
C1, C2: 100nF; C0805
C3, C4: 1nF; C0805
J1, J2, J3, J4, J5, J7, J8, J9: CONN_10X2SMT; 2X10_SMT
J6: USB_B_PTH; USB-B-PTH
L1: L-EUL2012C; L2012C
LED1, LED2: LEDSML0805; SML0805
R1, R2, R9, R10, R11, R12: 10k; R0603
R3: R-EU_R0603; R0603
R4: 240; R0603
R5, R6: 27R; R0603
R7, R8: 1k; R0603
RN1, RN2, RN3, RN4, RN5, RN6, RN7, RN8, RN9, RN10, RN13, RN14: 4R-N0603-ARV; 0603-ARV
S1: DIP-04SMD; DIPSWITCH-04-SMD
U1: P2X8C4M64P; TQFP100
U2: 25F32006WSOI; SO08-EIAJ
U3: FT231XS; SSOP20_L
U$2: MICRO_SD_CONNECTORMOLEX_HINGE; MICRO_SD
Y1: CRYSTALSMD-5X3.2-2PAD; CRYSTAL-SMD-5X3.2-2PAD

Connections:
BOOT_MISO: R4.1, U1.92 (P58), U2.2 (MISO)
BOOT_MOSI: S1.3 (3A), S1.4 (4A), U1.93 (P59), U2.5 (MOSI), U$2.3 (DIN)
BOOT_SCLK: U1.95 (P60), U2.6 (SCK), U$2.2 (CS)
CBUS0: LED1.C, U3.18 (CBUS0)
CBUS1: LED2.C, U3.17 (CBUS1)
D_M: J6.D-, R5.2
D_P: J6.D+, R6.2
FLASH_CS: R1.1, S1.2 (2A), U2.1 (CS)
GND: C1.2, C2.2, J1.1, J1.2, J1.19, J1.20, J2.1, J2.2, J2.19, J2.20, J3.1, J3.2, J3.19, J3.20, J4.1, J4.2, J4.3, J4.4, J5.1, J5.2, J5.19, J5.20, J6.GND, J6.SHLD1 (SHIELD), J6.SHLD2 (SHIELD), J7.1, J7.2, J7.19, J7.20, J8.1, J8.2, J8.19, J8.20, J9.1, J9.2, J9.3, J9.4, R2.2, U1.1 (TEST), U1.EPAD (GND), U2.4 (GND), U3.6 (GND), U3.16 (GND), U$2.6 (GND)
GPIO0: J3.3, J8.4, RN9.1
GPIO1: J3.4, J8.3, RN9.2 (1)
GPIO2: J3.5, J8.6, RN9.3 (1)
GPIO3: J3.6, J8.5, RN9.4 (1)
GPIO4: J3.7, J8.8, RN10.1
GPIO5: J3.8, J8.7, RN10.2 (1)
GPIO6: J3.9, J8.10, RN10.3 (1)
GPIO7: J3.10, J8.9, RN10.4 (1)
I2C_SCL0: J2.3, J7.4, RN3.1
I2C_SCL1: J2.5, J7.6, RN3.3 (1)
I2C_SCL2: J2.7, J7.8, RN4.1
I2C_SCL3: J2.9, J7.10, RN4.3 (1)
I2C_SDA0: J2.4, J7.3, RN3.2 (1)
I2C_SDA1: J2.6, J7.5, RN3.4 (1)
I2C_SDA2: J2.8, J7.7, RN4.2 (1)
I2C_SDA3: J2.10, J7.9, RN4.4 (1)
LED1: LED1.A, R7.2
LED2: LED2.A, R8.2
unnamed: R2.1, S1.5 (4B)
unnamed: R3.1, S1.6 (3B)
unnamed: R4.2, U$2.7 (DOUT)
P0: RN1.8 (2), U1.3 (P0)
P1: RN1.7 (2), U1.4 (P1)
P2: RN1.6 (2), U1.6 (P2)
P3: RN1.5 (2), U1.7 (P3)
P4: RN2.8 (2), U1.9 (P4)
P5: RN2.7 (2), U1.10 (P5)
P6: RN2.6 (2), U1.12 (P6)
P7: RN2.5 (2), U1.13 (P7)
P8: RN7.8 (2), U1.15 (P8)
P9: RN7.7 (2), U1.16 (P9)
P10: RN7.6 (2), U1.18 (P10)
P11: RN7.5 (2), U1.19 (P11)
P12: RN8.8 (2), U1.21 (P12)
P13: RN8.7 (2), U1.22 (P13)
P14: RN8.6 (2), U1.24 (P14)
P15: RN8.5 (2), U1.25 (P15)
P16: RN3.8 (2), U1.27 (P16)
P17: RN3.7 (2), U1.28 (P17)
P18: RN3.6 (2), U1.30 (P18)
P19: RN3.5 (2), U1.31 (P19)
P20: RN4.8 (2), U1.33 (P20)
P21: RN4.7 (2), U1.34 (P21)
P22: RN4.6 (2), U1.36 (P22)
P23: RN4.5 (2), U1.37 (P23)
P24: RN5.8 (2), U1.39 (P24)
P25: RN5.7 (2), U1.40 (P25)
P26: RN5.6 (2), U1.42 (P26)
P27: RN5.5 (2), U1.43 (P27)
P28: RN6.8 (2), U1.45 (P28)
P29: RN6.7 (2), U1.46 (P29)
P30: RN6.6 (2), U1.48 (P30)
P31: RN6.5 (2), U1.49 (P31)
P32: RN9.8 (2), U1.53 (P32)
P33: RN9.7 (2), U1.54 (P33)
P34: RN9.6 (2), U1.56 (P34)
P35: RN9.5 (2), U1.57 (P35)
P36: RN10.8 (2), U1.59 (P36)
P37: RN10.7 (2), U1.60 (P37)
P38: RN10.6 (2), U1.62 (P38)
P39: RN10.5 (2), U1.63 (P39)
P40: RN13.8 (2), U1.65 (P40)
P41: RN13.7 (2), U1.66 (P41)
P42: RN13.6 (2), U1.68 (P42)
P43: RN13.5 (2), U1.69 (P43)
P44: RN14.8 (2), U1.71 (P44)
P45: RN14.7 (2), U1.72 (P45)
P46: RN14.6 (2), U1.74 (P46)
P47: RN14.5 (2), U1.75 (P47)
P48: U1.77 (P48)
P49: U1.78 (P49)
P50: U1.80 (P50)
P51: U1.81 (P51)
P52: U1.83 (P52)
P53: U1.84 (P53)
P54: U1.86 (P54)
P55: U1.87 (P55)
P56: U1.89 (P56)
P57: U1.90 (P57)
P62: C3.1, R11.1, U1.98 (P62)
P63: C4.1, R12.1, U1.99 (P63)
PWM0: J3.11, J8.12, RN13.1
PWM1: J3.12, J8.11, RN13.2 (1)
PWM2: J3.13, J8.14, RN13.3 (1)
PWM3: J3.14, J8.13, RN13.4 (1)
PWM4: J3.15, J8.16, RN14.1
PWM5: J3.16, J8.15, RN14.2 (1)
PWM6: J3.17, J8.18, RN14.3 (1)
PWM7: J3.18, J8.17, RN14.4 (1)
RESET_N: S1.1 (1A), U1.100 (RESN)
SD_CLK: S1.7 (2B), U1.96 (P61), U$2.5 (SCLK)
SPI_MISO0: J1.5, J5.6, RN1.3 (1)
SPI_MISO1: J1.9, J5.10, RN2.3 (1)
SPI_MISO2: J1.13, J5.14, RN7.3 (1)
SPI_MISO3: J1.17, J5.18, RN8.3 (1)
SPI_MOSI0: J1.4, J5.3, RN1.2 (1)
SPI_MOSI1: J1.8, J5.7, RN2.2 (1)
SPI_MOSI2: J1.12, J5.11, RN7.2 (1)
SPI_MOSI3: J1.16, J5.15, RN8.2 (1)
SPI_SCLK0: J1.3, J5.4, RN1.1
SPI_SCLK1: J1.7, J5.8, RN2.1
SPI_SCLK2: J1.11, J5.12, RN7.1
SPI_SCLK3: J1.15, J5.16, RN8.1
SPI_SS0: J1.6, J5.5, RN1.4 (1)
SPI_SS1: J1.10, J5.9, RN2.4 (1)
SPI_SS2: J1.14, J5.13, RN7.4 (1)
SPI_SS3: J1.18, J5.17, RN8.4 (1)
UART_RX0: J2.11, J7.12, RN5.1
UART_RX1: J2.13, J7.14, RN5.3 (1)
UART_RX2: J2.15, J7.16, RN6.1
UART_RX3: J2.17, J7.18, RN6.3 (1)
UART_TX0: J2.12, J7.11, RN5.2 (1)
UART_TX1: J2.14, J7.13, RN5.4 (1)
UART_TX2: J2.16, J7.15, RN6.2 (1)
UART_TX3: J2.18, J7.17, RN6.4 (1)
USBDM: R5.1, U3.12 (USBDM)
USBDP: R6.1, U3.11 (USBDP)
USB_3V3: C1.1, U3.3 (VCCIO), U3.13 (3V3OUT), U3.14 (!RESET)
USB_5V: C2.1, L1.2, R7.1, R8.1, U3.15 (VCC)
USB_RX: C3.2, R10.2, R11.2, U3.4 (RXD)
USB_TX: C4.2, R9.2, R12.2, U3.20 (TXD)
U_1V8: J4.5, J4.6, J4.7, J4.8, J9.5, J9.6, J9.7, J9.8, U1.2 (VDD), U1.8 (VDD), U1.14 (VDD), U1.20 (VDD), U1.26 (VDD), U1.32 (VDD), U1.38 (VDD), U1.44 (VDD), U1.52 (VDD), U1.58 (VDD), U1.64 (VDD), U1.70 (VDD), U1.76 (VDD), U1.82 (VDD), U1.88 (VDD), U1.94 (VDD)
U_3V3: J4.9, J4.10, J4.11, J4.12, J9.9, J9.10, J9.11, J9.12, R1.2, R3.2, R9.1, R10.1, U1.5 (V0003), U1.11 (V0407), U1.17 (V0811), U1.23 (V1215), U1.29 (V1619), U1.35 (V2023), U1.41 (V2427), U1.47 (V2831), U1.55 (V3235), U1.61 (V3639), U1.67 (V4043), U1.73 (V4447), U1.79 (V4851), U1.85 (V5255), U1.91 (V5659), U1.97 (V6063), U2.3 (WP), U2.7 (HOLD), U2.8 (VCC), U$2.4 (VDD)
U_5V: J4.13, J4.14, J4.15, J4.16, J9.13, J9.14, J9.15, J9.16
U_IN: J4.17, J4.18, J4.19, J4.20, J9.17, J9.18, J9.19, J9.20
VBUS: J6.VBUS, L1.1
XIN: U1.51 (XI), Y1.P$2 (2)
XOUT: U1.50 (XO), Y1.P$1 (1)



Board: 2 copper layers, 100.0 x 100.0 mm, 46 parts (11 on the bottom side), 127 nets.

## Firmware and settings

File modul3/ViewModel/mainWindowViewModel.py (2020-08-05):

from PyQt5 import QtWidgets, QtCore, uic, QtGui
from pyqtgraph import PlotWidget,GraphicsLayoutWidget
from View.channelControlView import channelControlView
from ViewModel.graphViewModel import graphViewModel
from ViewModel.appConfig import appConfig
from Model.streamManager import StreamManager
from Model.streamManager import StreamParser
from ViewModel.connectionViewModel import ConnectionViewModel
from ViewModel.calibGraphViewModel import CalibGraphViewModel
from ViewModel.analyseViewModel import AnalyseViewModel
import pyqtgraph as pg
import numpy as np
import bisect

class MainWindowViewModel(QtWidgets.QMainWindow):
    # custom signals
    mySignal = QtCore.pyqtSignal()
    myBoolSignal = QtCore.pyqtSignal(bool)

    def __init__(self, *args, **kwargs):
        super(MainWindowViewModel, self).__init__(*args, **kwargs)
        self.config = appConfig() 
        #Load the UI Page
        uic.loadUi('./View/mainWindow.ui', self)
        self.initChannelControlView(self.config.chnConfigs)
        self.initGraphView(self.graphView) # pass the handel to the graphViewModel
        self.initControls()
        self.initStreamManager()
        self.initConnectionViewModel()
        self.initCalibGraphViewModel()
        self.initAnalysisViewModel()
        # connections
        #self.channelControlView.channelSettingChanged.connect(self.graphViewModel.updateChannelSettings)
        self.channelControlView.channelSettingChanged.connect(self.changeConfig)
        self.saveConfigButton.clicked.connect(self.saveConfig)
        self.startStopStreamButton.toggled.connect(self.startStopStream)
        self.streamManager.dataUpdated.connect(self.updateGraphData)
        self.calibGraphViewModel.newCalibValues.connect(self.updateChannelCalib)
        self.resetStreamButton.clicked.connect(self.resetStream)
        self.menuExportRawData.triggered.connect(self.exportRawData)

    def initCalibGraphViewModel(self):
        self.calibGraphViewModel = CalibGraphViewModel(self.calibGraphView,self.calibControlFrame)

    def initConnectionViewModel(self):
        self.connectionViewModel = ConnectionViewModel(self.connectionTab)

    def initChannelControlView(self,config):
        self.channelControlView = channelControlView(config)
        self.scrollArea.setWidget(self.channelControlView)

    def initGraphView(self,graphView):
        self.graphViewModel = graphViewModel(graphView,self.config,self.channelControlView)
    
    def initControls(self):
        conf = self.config
        self.stackedGraphRadioButton.setChecked(conf.isStacked)
        self.stackedGraphRadioButton.toggled.connect(self.plotLayoutChanged)
        self.unifiedGraphRadioButton.setChecked(not conf.isStacked)
        self.multiAxisCheckBox.setChecked(conf.isMultiAxis)

    def initAnalysisViewModel(self):
        #self.tabWidget.setTabEnabled(3,False)
        self.analysisViewModel = AnalyseViewModel(self.tabWidget,self.config)
    def initStreamManager(self):
        self.streamManager = StreamManager()

    def startStopStream(self,enable):
        print(len(self.streamManager.numData[0]))
        if enable:
            self.startStopStreamButton.setText("Stop Stream")
            self.streamManager.startStream(self.getStreamConfig())
            self.tabWidget.setTabEnabled(3,False)
            self.resetStreamButton.setEnabled(False)
        else:
            self.startStopStreamButton.setText("Start Stream")
            self.streamManager.stopStream()
            self.tabWidget.setTabEnabled(3,True)
            self.resetStreamButton.setEnabled(True)

    def getStreamConfig(self):
        if self.fileStreamRadioButton.isChecked():
            config = {"streamType":"FileStream","filePath":self.connectionViewModel.filePathLineEdit.text()}
            return config
        elif self.serialStreamRadioButton.isChecked():
            config = {"streamType":"SerialStream","serialPort":self.serialComboBox.currentText()}
            return config

    def saveConfig(self):
        self.config.saveConfig()
        self.saveConfigButton.setEnabled(False)

    def changeConfig(self,chnNum,ctl,text):
        self.graphViewModel.updateChannelSettings(chnNum,ctl,text)
        self.config.changeConfig(chnNum,ctl,text)
        self.saveConfigButton.setEnabled(True)

    def plotLayoutChanged(self,isStacked):
        self.config.changeGraphLayout(isStacked)
        self.graphViewModel.clearGraphView()
        
        if isStacked:
            self.graphViewModel.drawStackedPlots()
        else:
            self.graphViewModel.drawUnifiedPlots()

    def updateGraphData(self):
        self.graphViewModel.update()

    def updateChannelCalib(self,chnNum,scale,offset):
        self.channelControlView.updateCalibration(chnNum,scale,offset)

    def resetStream(self):
        StreamManager.rawData = bytearray()
        StreamManager.numData = [[],[],[],[],[],[],[],[],[]]
        StreamParser.seeker_position = 0
        StreamParser.rawPackage = bytearray()
        self.updateGraphData()

    def exportRawData(self):
        path = QtGui.QFileDialog.getSaveFileName(self, 'data.raw')
        print(path[0])
        if not (path==''):
            with open(path[0],'wb') as file:
                with StreamManager.dataLock:
                    file.write(StreamManager.rawData)

    def importCSVfile(self):
        pass
        

    """ def plot(self, hour, temperature):
        self.graphWidget.plot(hour, temperature)
        vb = self.graphWidget.getViewBox()
        #vb.setMouseMode(pg.ViewBox.RectMode)
        # only zoom on x axis
        self.graphWidget.setMouseEnabled(y=False)                                                          
        # auto update y axis to visible min max values
        self.graphWidget.sigRangeChanged.connect(self.update_y_axis)  """
        
        
        

    # custom slots
    """ def pushButton_clicked(self):
        print("Click!")
        self.myBoolSignal.emit(False)
    
    def mySignalEmitted(self):
        print("Emitted!")

    def inf1_restrict_position(self):
        idx = min(bisect.bisect_left(self.data[0],self.inf1.getXPos()),len(self.data[0])-1)
        self.inf1.setPos([self.data[0][idx],0])
        self.inf1.label.setFormat('y={:0.2f}'.format(self.data[1][idx])) """

    """ def update_y_axis(self): """
        # fancy code to update y axis to min max values when only x zooming is enabled
    """ self.graphWidget.sigRangeChanged.disconnect(self.update_y_axis) 
        vb = self.graphWidget.getViewBox()
        xRange = vb.viewRange()[0]
        print(xRange)
        idyL = min(bisect.bisect_left(self.data[0],xRange[0]),len(self.data[0])-1)
        idyH = min(bisect.bisect_left(self.data[0],xRange[1]),len(self.data[0])-1)
        print(self.data[1][idyL],self.data[1][idyH])
        print(min(self.data[1][idyL:idyH]))
        vb.setYRange(min(self.data[1][idyL:idyH]),max(self.data[1][idyL:idyH]))
        self.graphWidget.sigRangeChanged.connect(self.update_y_axis)  """

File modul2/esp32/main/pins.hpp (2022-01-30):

// Copyright: 2021, Diez B. Roggisch, Berlin, all rights reserved

#pragma once

#include "hal/gpio_types.h"

#define PIN_NUM_OTA gpio_num_t(0)

// Pin mapping when using SPI mode.
// With this mapping, SD card can be used both in SPI and 1-line SD mode.
// Note that a pull-up on CS line is required in SD mode.

#define PIN_NUM_MISO gpio_num_t(2)
#define PIN_NUM_MOSI gpio_num_t(15)
#define PIN_NUM_CLK  gpio_num_t(14)
#define PIN_NUM_CS   gpio_num_t(13)

#define PIN_NUM_START gpio_num_t(26)

#define SDA gpio_num_t(26)
#define SCL gpio_num_t(27)

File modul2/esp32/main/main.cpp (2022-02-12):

#include "pins.hpp"
#include "sdcard.hpp"
#include "mqtt.hpp"
#include "events.hpp"

#include "wifi.hpp"
#include "buttons.hpp"
#include "smartconfig.hpp"

#include <esp_log.h>
#include <freertos/FreeRTOS.h>
#include <freertos/task.h>
#include <driver/spi_master.h>
#include <sstream>
#include <condition_variable>

extern "C" void app_main();

#define TAG "main"

namespace {

}

void app_main()
{
  ESP_ERROR_CHECK(esp_event_loop_create_default());
  deets::buttons::setup({
       { PIN_NUM_OTA, deets::buttons::pull_e::UP, deets::buttons::irq_e::NEG }
    });

  std::mutex m;
  std::condition_variable cv;


  unifhy::events::buttons::register_button_callback(
    unifhy::events::buttons::OTA,
    [&cv](unifhy::events::buttons::button_events_t) {
      if(deets::wifi::connected())
      {
        ESP_LOGI(TAG, "Connected to WIFI, run write");
        cv.notify_one();
      }
      else
      {
        ESP_LOGI(TAG, "Not connected to WIFI, running smartconfig");
        deets::smartconfig::run();
      }
    }
    );

  deets::wifi::setup();

  unifhy::sdcard::SDCardWriter writer;
  unifhy::mqtt::MQTTClient mqtt_client;

  for( ;; )
  {
    std::unique_lock<std::mutex> lk(m);
    cv.wait(lk);
    const auto [ name, count, start, end ] = writer.write_file(2048, 5);
    std::stringstream ss;
    ss << name << ":count=" << count << ":start=" << start << ":end=" << end;
    mqtt_client.publish("write_rate", ss.str().c_str());
  }
}

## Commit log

2020-02-29 Initial commit - 500us loop with 9 long words SPI communication
2020-02-29 Switch to different SPI channel and hardware CS
2020-02-29 Add arduino layer as component
2020-02-29 Introduce data-logger and signal sampler task
2020-08-05 Convert data sampler into class
2020-08-05 Move ESP32 test balloon into own subdirectory
2020-08-05 First commit of Modul3 Software
    [F.csv, RQOBS_data_full.csv, data.csv]
2020-08-05 Datenblatt des ADC
2020-09-29 RQ2 commit #1
    New Eagle boards and schematics, RedQueen 2 mainboard and supply
    [RQ2_mainboard.brd, RQ2_mainboard.sch, RQ2_supply.brd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]
2021-03-05 Add some documentation about the ADS1256 breakout board
2021-03-05 P2 hello world with extra serial
    The extra serial is because I currently can't flash but only load to
    memory.
2021-05-30 Implement the R command
    This allows to set the samplerate
2021-05-30 Add P2 Eval Board schematic
2021-06-05 Basic SD card writing works
    Currently the 30K SPS mode does not seem to properly work, but
    we *do* write stuff!
2021-06-18 Fix linesize and report SD card status via LED
2021-06-18 DROPME: Mark block-writing with pin
2021-06-20 Start Connector Implementation
2021-06-27 Add HyperRAM driver
2021-07-03 changed variable name to enable compilation with Propeller Tool
2021-07-03 just some minor changes to enable compiling with Propeller Tool
2021-07-04 Test pin reading
2021-07-04 Trigger data acquisition by button
2021-07-04 Introduce SD card and write to it based on the second button
2021-07-04 Fix bug with not waiting for serial streaming to finish
    [read-sequential-files.py]
2021-07-08 Upper case filenames
2021-07-08 Adapt code to the new base for the accessory boards
2021-10-12 Introduce configuration object
    This depends on a preprocessor variable to select the target board
2021-10-14 Begin working on switched frontend
2021-10-14 Introduce capturing switch
2021-10-18 Implement switched frontend
2021-10-18 Intorduce and use convenience method to set the samplerate
    Also improve flashtime by making the ADC buffer smaller - it
    was inflated during debugging.
2021-10-18 Fall out of capturing when the capacity is exhausted
2022-01-02 Begin cleanup of SD card driver
2022-01-02 wip: debug pin to signify the start of the driver
2022-01-30 Move toward ESP SDK 4.2 in an attempt to get faster SD card writes
    [partitions.csv]
2022-02-12 Enhance sd card writing code based on my ESP32 investigation
2022-02-12 Write based on button-press for simple recording workflow
2022-02-20 Add KiCad project from mainboard
    [RQ2_mainboard_v0.2.kicad_pcb, RQ2_mainboard_v0.2.sch]
2022-02-20 Add supply board
    [RQ2_supply.sch]
2022-03-29 Comment about maximum SPI speed on P2 Eval Rev C
2022-03-29 Clarified mount code
2022-03-29 Hook my SD SPI code into FAT32
2022-03-30 Fix mountPartition to do what it promises to do and use it
2023-04-19 RQ2 archived versions
    [RQ2_analog_v0.1.brd, RQ2_analog_v0.1.sch, RQ2_mainboard_v0.2.brd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]
2023-04-19 RQ2 v1.0 files
    [RQ2_analog.brd, RQ2_analog.sch, RQ2_mainboard.brd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]
2023-08-27 Place current version of RQ into repo
    [RQ2_mainboard_v0.2.kicad_sch, RQ2_supply.kicad_pcb]
2023-08-27 Get switched frontend working again

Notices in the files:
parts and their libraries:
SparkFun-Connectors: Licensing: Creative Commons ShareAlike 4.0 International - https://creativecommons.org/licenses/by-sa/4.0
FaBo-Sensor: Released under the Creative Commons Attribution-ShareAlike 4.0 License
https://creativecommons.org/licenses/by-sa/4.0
